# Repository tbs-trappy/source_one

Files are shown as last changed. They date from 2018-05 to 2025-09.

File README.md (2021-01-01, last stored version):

# source_one
Open Source FPV Drone Frame project initiated by Team BlackSheep
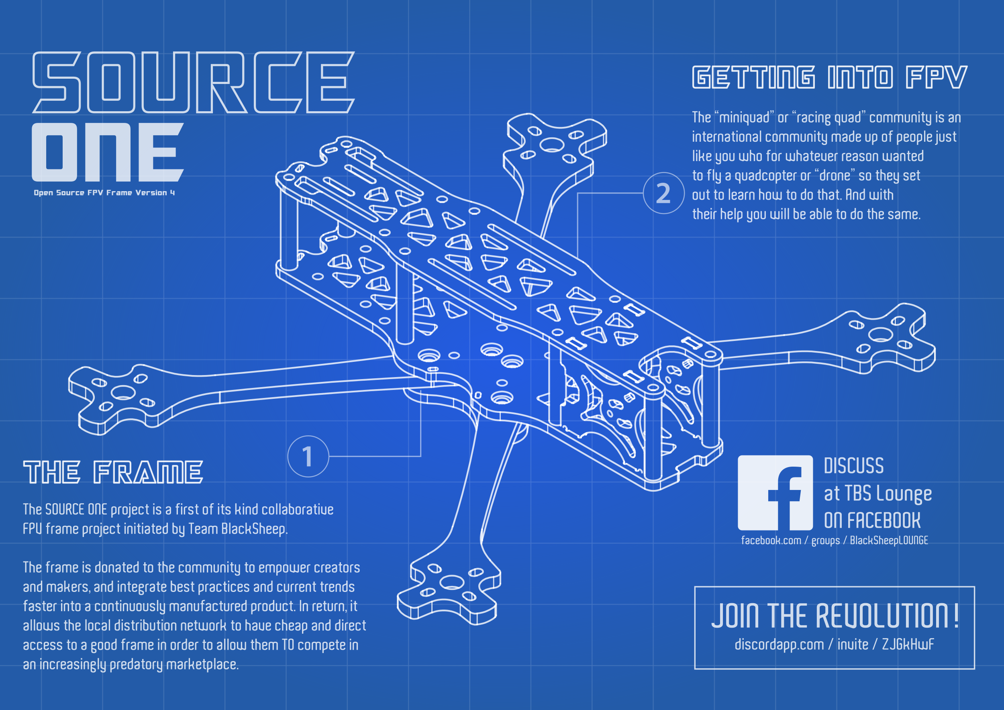
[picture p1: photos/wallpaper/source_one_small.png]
[](https://github.com/tbs-trappy/source_one/blob/master/photos/wallpaper/source_one.png)

# About SOURCE ONE
## The idea
The SOURCE ONE is the first of its kind, open source collaborative frame project. It empowers the community to integrate best practices and current trends into a continuously manufactured FPV frame. The price, documentation and compatibility puts it on track to be the most accessible frame for newcomers and professionals alike.

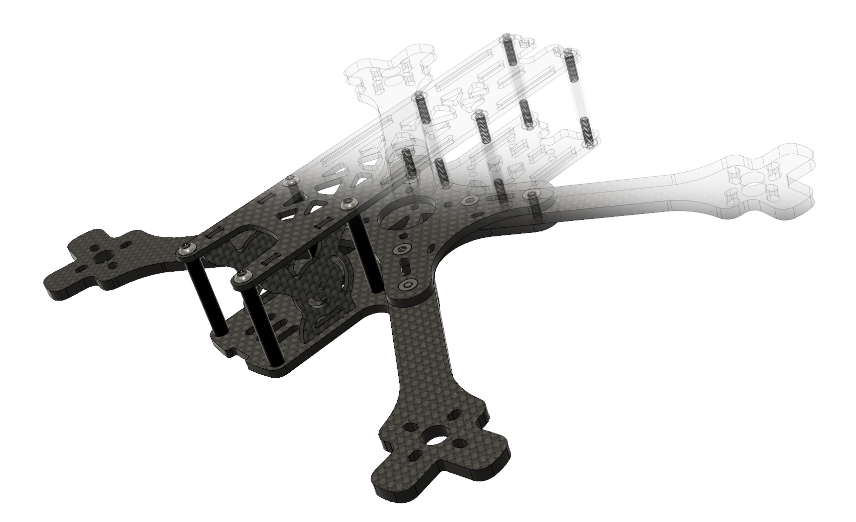
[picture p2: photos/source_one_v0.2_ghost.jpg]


## Frame specifications
* Wheelbase 5": 226mm
* Wheelbase 7": 318mm
* Top plate: 2mm
* Bottom plate 3mm
* Standoff height: 30mm
* Arm thickness 5": 4mm
* Arm thickness 7": 6mm
* Stack mounting: 30.5 × 30.5mm & 20 x 20
* Weight 5": 99.5g

## Hardware
* 24x M3x10 allen screw
* 4x M3x14 allen screw
* 8X OD 5mm M3 30mm standoff
* 6x M3 press insert nut

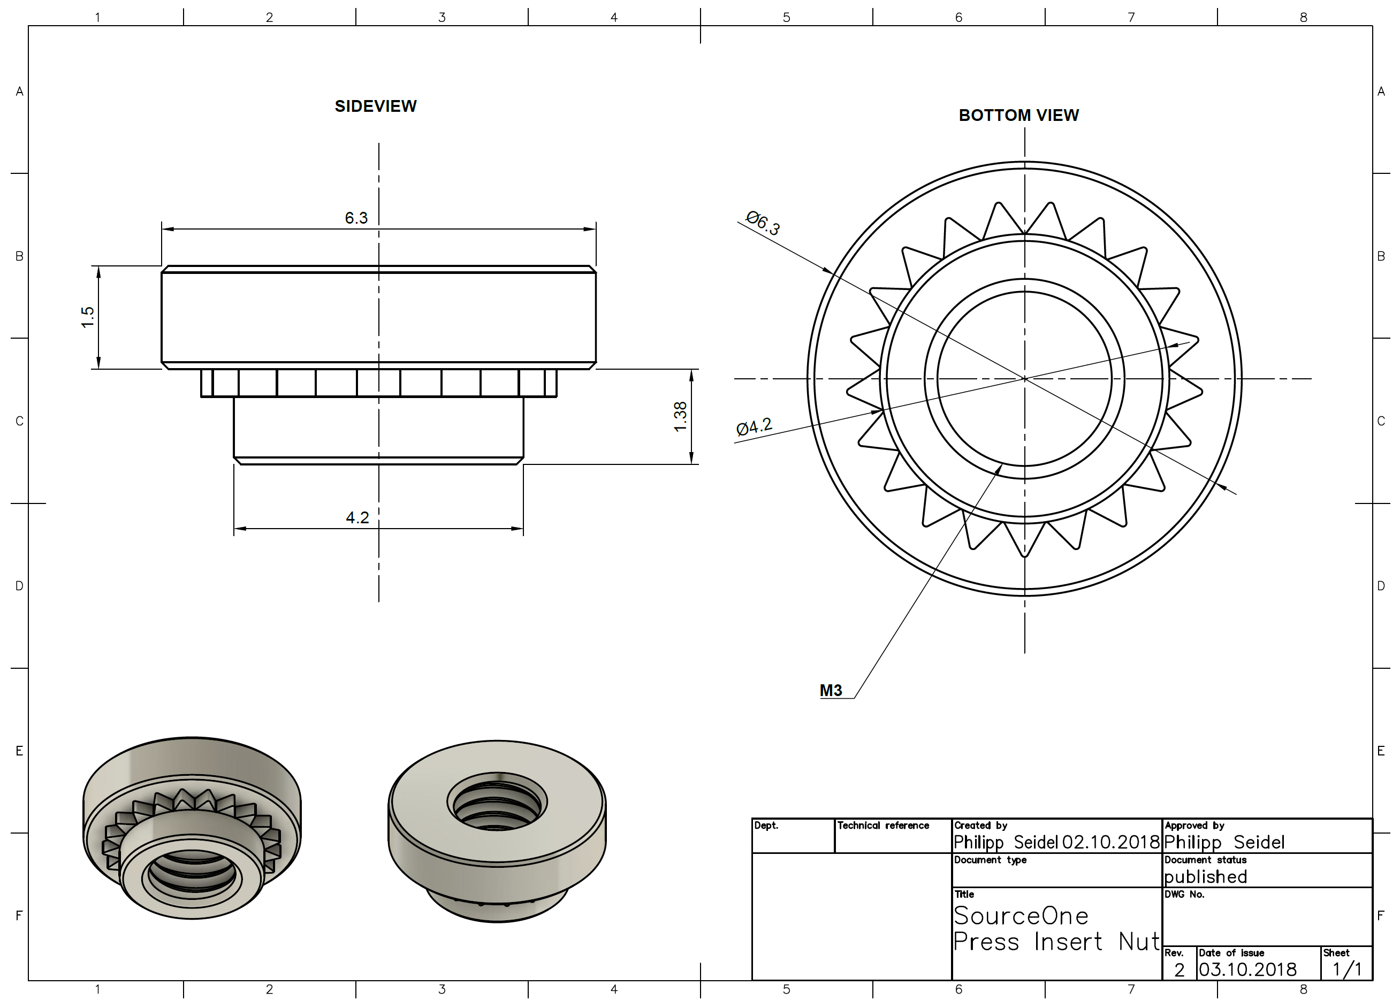
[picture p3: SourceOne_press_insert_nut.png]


## Project links
* Project discussion: https://discordapp.com/invite/ZJGkHwF 
* Project files: https://github.com/tbs-trappy/source_one 
* 3D-printed accessories: https://www.thingiverse.com/tag:sourceone

Please use the tag "sourceone" when uploading files to thingiverse.com

## Where to buy
* [www.team-blacksheep.com](https://team-blacksheep.com/products/prod:source_one_5in)
* [www.racequadgear.de](https://www.racequadgear.de/TBS-SOURCE-ONE-5)
* [www.n-factory.de](https://n-factory.de/TBS-SOURCE-ONE-5)
* [www.redbee.de](https://redbee.de/TBS-Source-ONE-5-VXXX)
* [www.defiancerc.com](https://www.defiancerc.com/products/tbs-source-one-5-v0-11)
* [www.ka-nickel.eu](https://ka-nickel.eu/produkt/tbs-source-one/)
* [www.phaserfpv.com.au](https://www.phaserfpv.com.au/products/tbssourceone5framekitv011)
* [www.multirotorshop.com](https://www.multirotorshop.com.au/product/tbs-source-one-v0-2-5inch/)
* [www.shop.brickracing.com](https://shop.brickracing.com/TBS-Source-One-V0.2-drone-frame)
* [www.skanehobby.se](https://www.skanehobby.se/shop/tbs-source-one-v0-2/)
* [www.juampifpv.com](https://www.juampifpv.com/index.php?pagina=detalle&idp=403)
* [www.killadrones.co.nz](https://www.killadrones.co.nz/store/TBS-Source-One-5-Inch-Frame-p137993332)
* [www.quadjunkie.co.nz](https://quadjunkie.co.nz/product-category/racing-freestyle-frames/tbs-source-one/)
* [www.drone-fpv-racer.com](https://www.drone-fpv-racer.com/en/dfr-source-one-5-frame-v3-3579.html)
* open [issue](https://github.com/tbs-trappy/source_one/issues/new) if you want your shop added

## Where to buy 3D printed parts
Here is a list of recommended 3D Printing services who are sharing their files under the GPL license (OpenSource). 
* [3dmatisse USA](http://bit.ly/3dmatisse_USA)
* [bmc3d.co](https://bmc3d.co/collections/all/source-one)

## Compatibility

| Part | v0.1| v0.11| v0.2| v3| v4|
| --- | --- | --- | --- | --- | --- |
| topplate |fits only v0.1 | | |fits all lower versions|fits only v4 | 
| bottompate |fits only v0.1 | |fits all lower versions|fits only v3 |fits only v4 | 
| arms | | | |fits all lower versions |fits only v4 | 
| centerplate |fits only v0.1 | |fits  v0.11 and v0.2 |fits only v3 |fits only v4 | 
| camplates |fits only v0.1 | | |fits all lower versions|fits only v4 | 
| battery pad |no pad available | |fits all lower versions|fits only v3 |fits only v4 | 

## Changelog
### SourceOne v4
* complete redesign
* DJI Airunits fits in the back

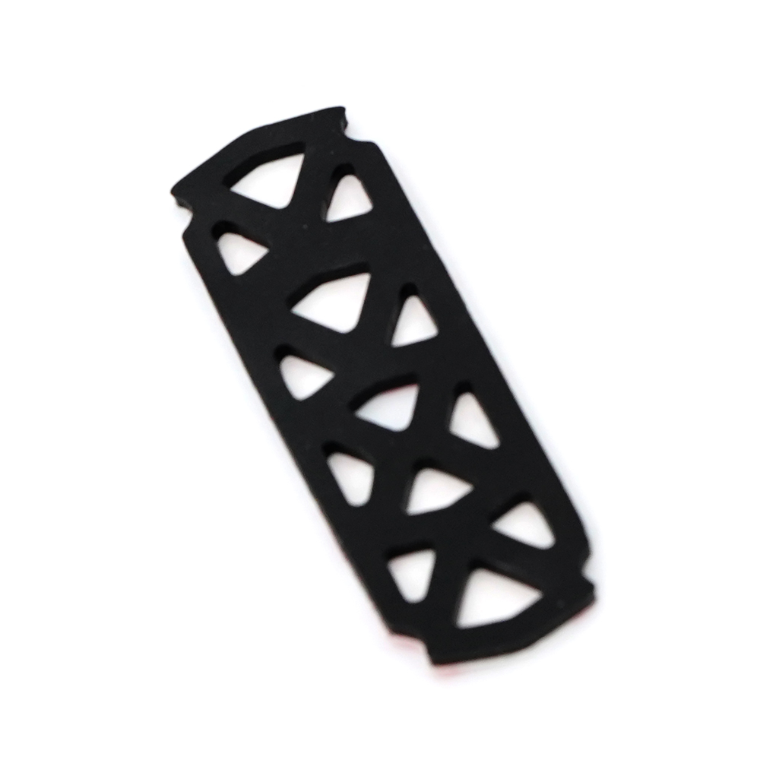
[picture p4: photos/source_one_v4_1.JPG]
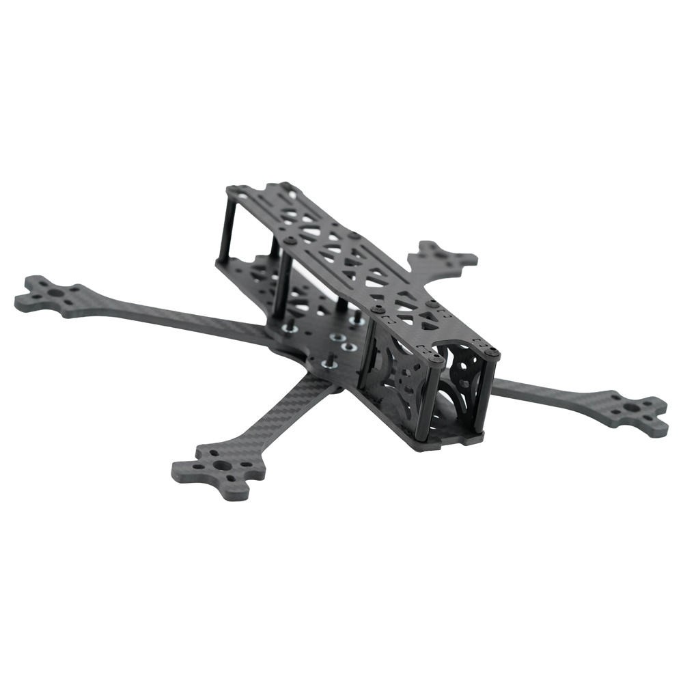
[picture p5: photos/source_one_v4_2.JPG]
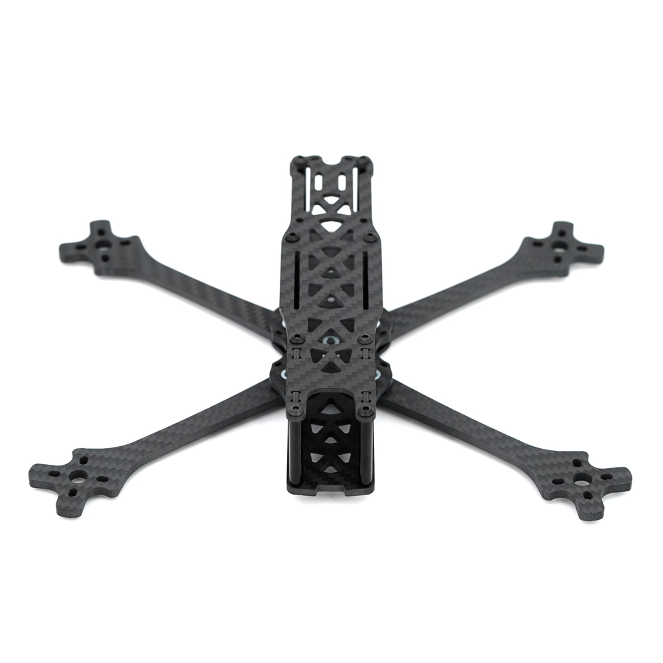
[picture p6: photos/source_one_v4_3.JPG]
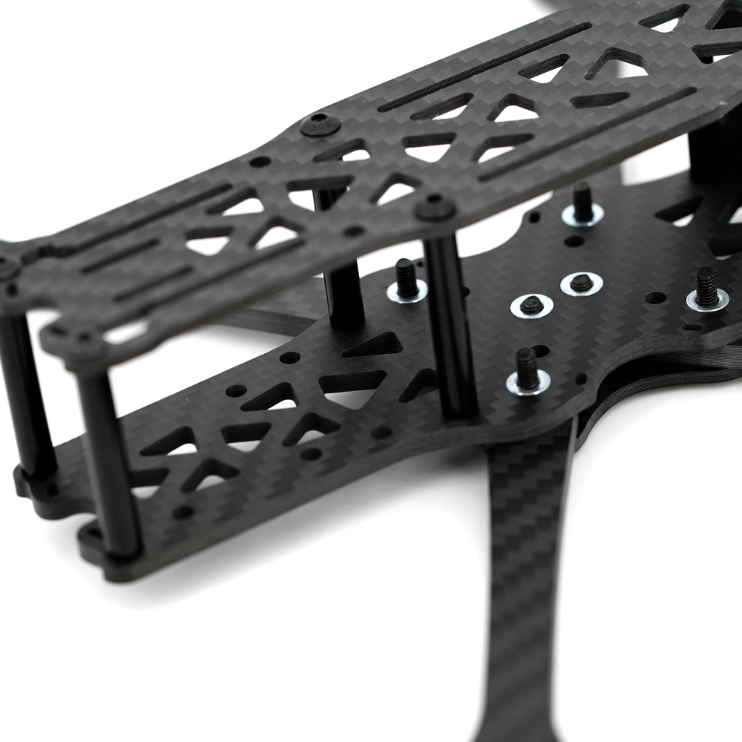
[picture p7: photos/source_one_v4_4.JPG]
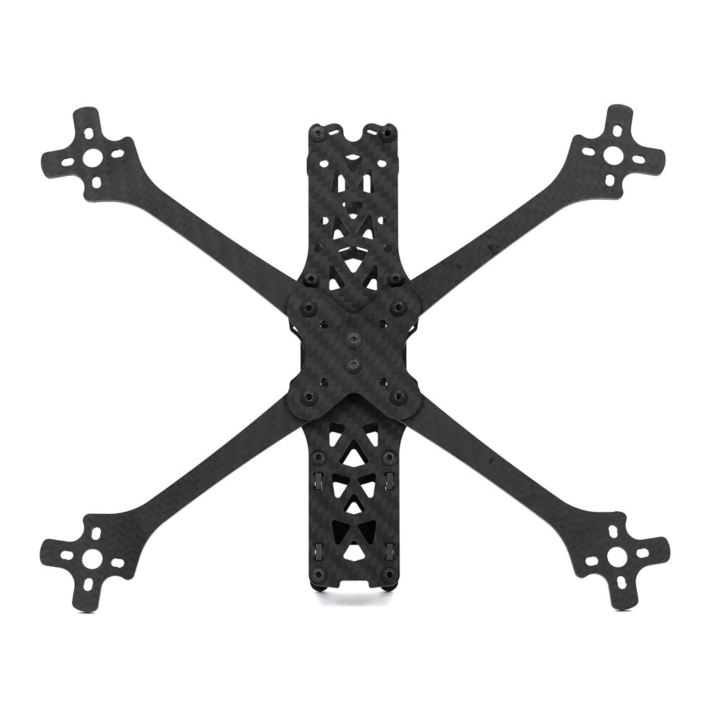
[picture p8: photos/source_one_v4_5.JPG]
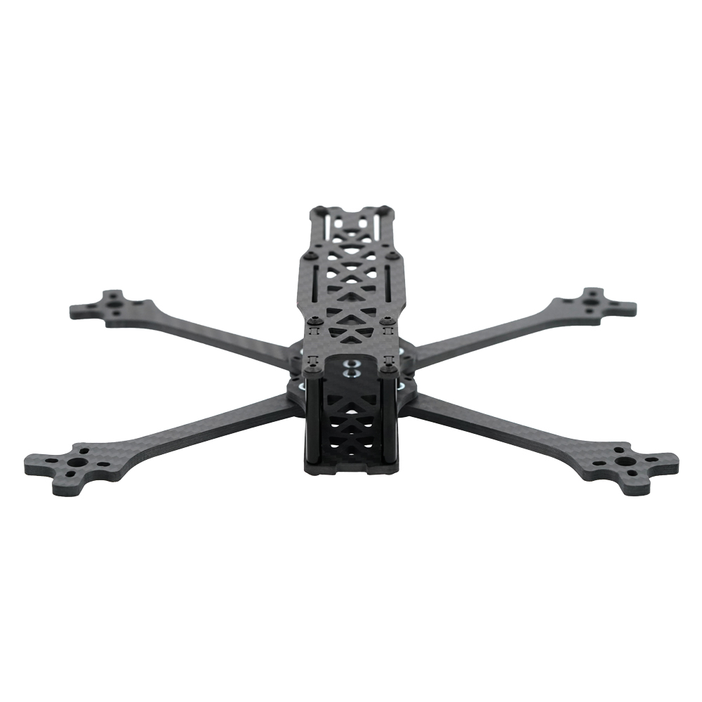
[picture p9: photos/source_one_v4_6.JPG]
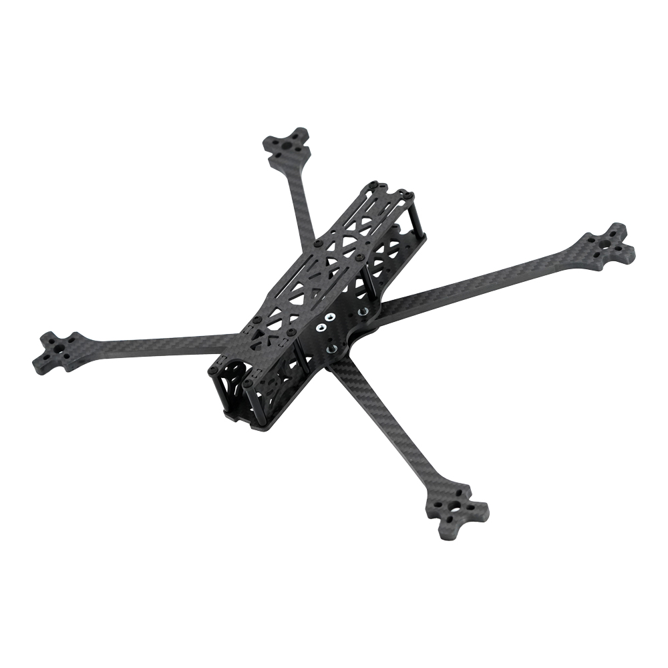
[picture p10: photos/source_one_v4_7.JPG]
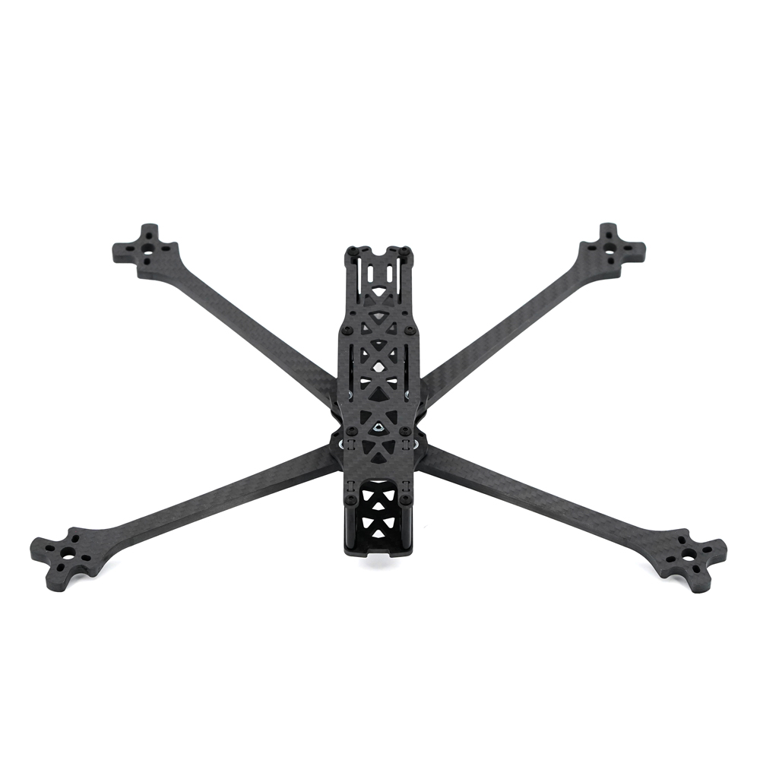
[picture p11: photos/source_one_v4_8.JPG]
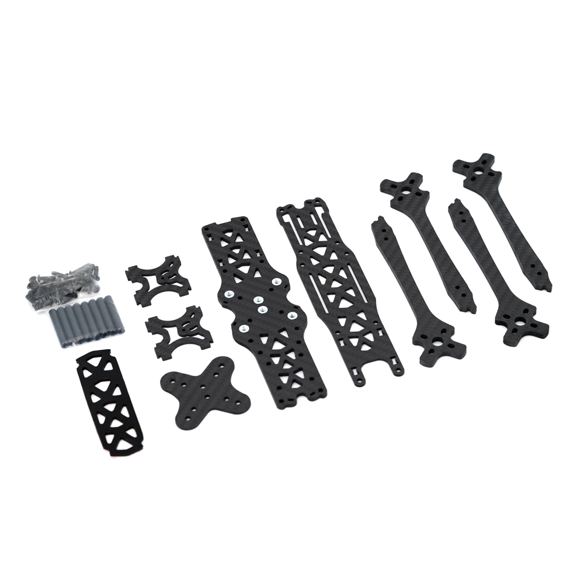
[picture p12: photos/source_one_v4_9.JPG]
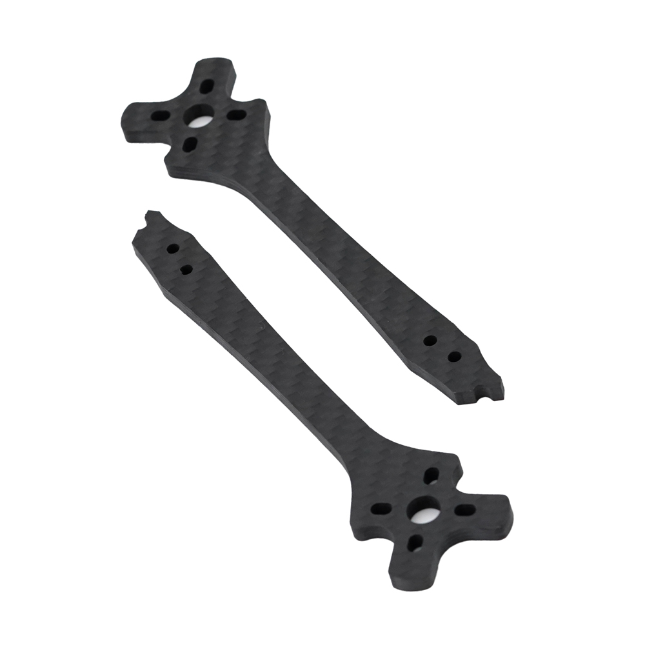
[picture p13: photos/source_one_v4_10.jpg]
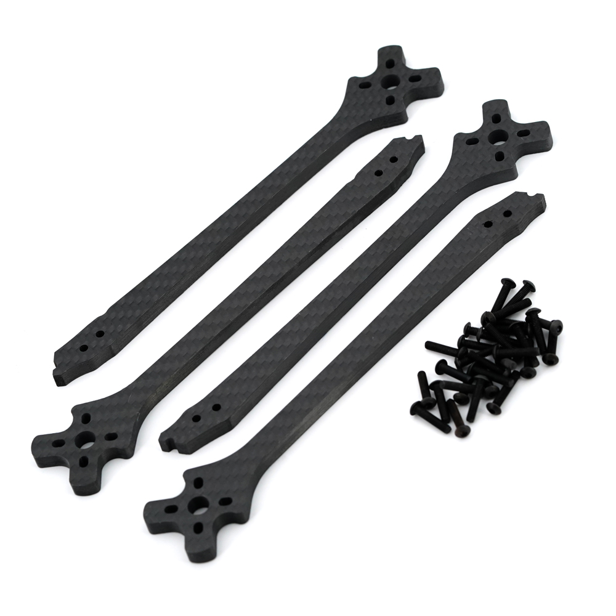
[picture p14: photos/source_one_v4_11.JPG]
          

### SourceOne v3
* new TopPlate, with longer Battery-strap slots - backwards compatible to V0.2
* new BatteryPad, cause of the repositioning and longer Battery-strap slots - NOT backwards compatible to V0.2
* new Cam-plate design, with Angel holes and a forward position, the Plate also contacts the 4 front Spacers for more rigidy in the front part - backwards compatible to V0.2
* Main-plate is now on top for more building room, a 20x20 (M2) mounting pattern added in the front, Antenna Zip-tie holes added - NOT backwards compatible to V0.2
* 5inch Arms got a reinforcement on the outer mounting hole (backwards compatible to V.01 and V0.2)
* new Bottom-plate - NOT backwards compatible to V0.2
* changed our versioning because its sounds better (we went from v0.2 straight to v3) 

that's all changes on the Carbon and the BatteryPad. For the guys that want to mount the Battery on the bottom, i made a small 3D-batterystrap mount, that also gives the battery a flat mounting option, cause of the swap of the Center and Bottom plate. All other 3D-Printed parts will fit the Version 0.3.

### SourceOne v0.2

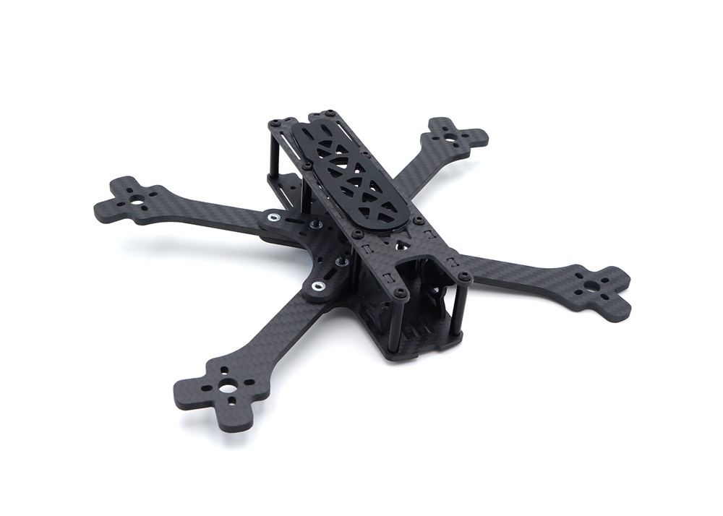
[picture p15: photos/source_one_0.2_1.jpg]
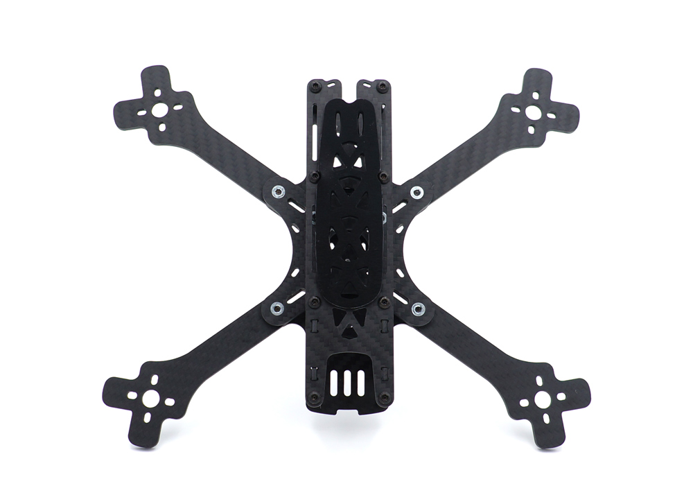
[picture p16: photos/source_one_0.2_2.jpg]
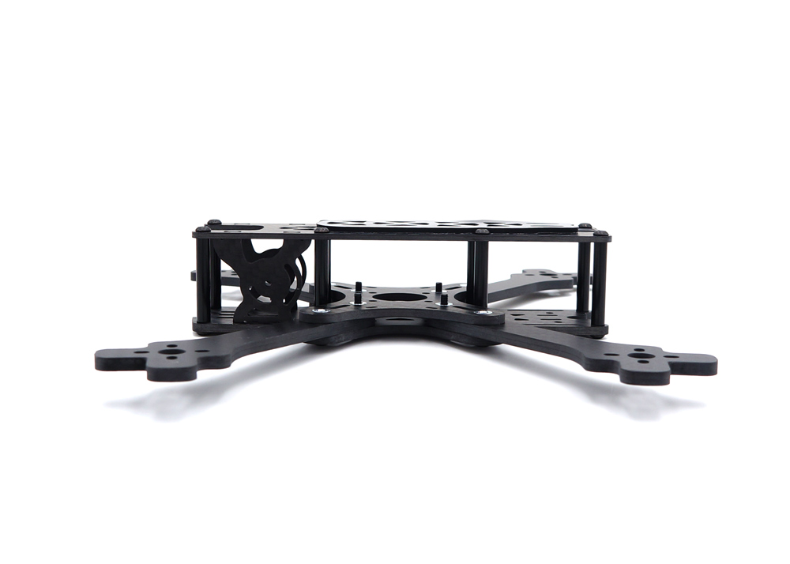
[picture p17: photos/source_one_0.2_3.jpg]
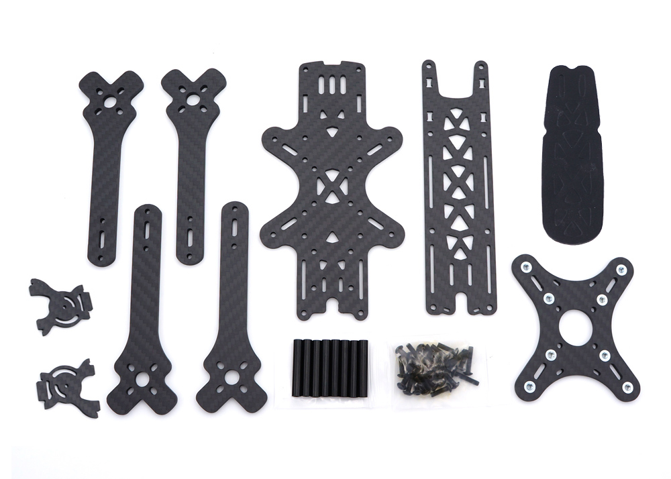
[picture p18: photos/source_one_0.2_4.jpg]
    

* top plate: new design pattern
* top plate: wider battery strap slots
* top plate: removed indentation near the second spacer row
* top plate: ziptie holes for RX Antennas
* center plate: ziptie holes for securing battery cable
* cam plate: new design
* added slots for MicroCam metal brackets
* bottom plate: micro cam bracket mounting slots
* bottom plate: 20x20 VTX stack holes
* 20x20 FC support
* arms: better motor protection
* arms: added 6 inch arms
* bottom battery mount slots for 20mm straps
* Impulse RC Wolf PDB support
* added silicone/foam battery pads (top & bottom)

#### compatibility
We changed the camera plate. Therefore topplate and bottomplate are not compatible with v0.11. Amrs and centerplate is compatible with v0.11

### SourceOne v0.11
* added press nuts
* define project leads and github commit rules
* define folder structure for acessories, variants, etc.
* define responsible people for maintaining manual, github website, graphics

### SourceOne v0.1

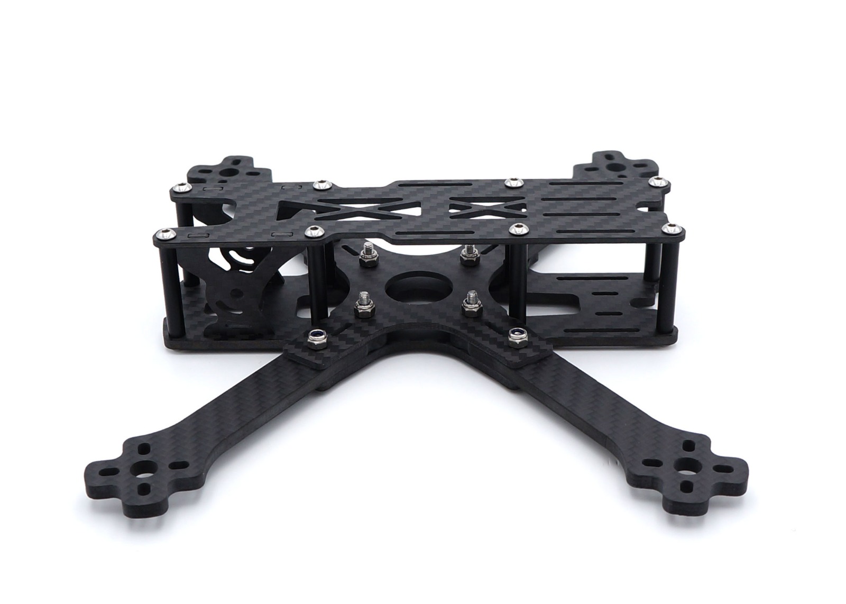
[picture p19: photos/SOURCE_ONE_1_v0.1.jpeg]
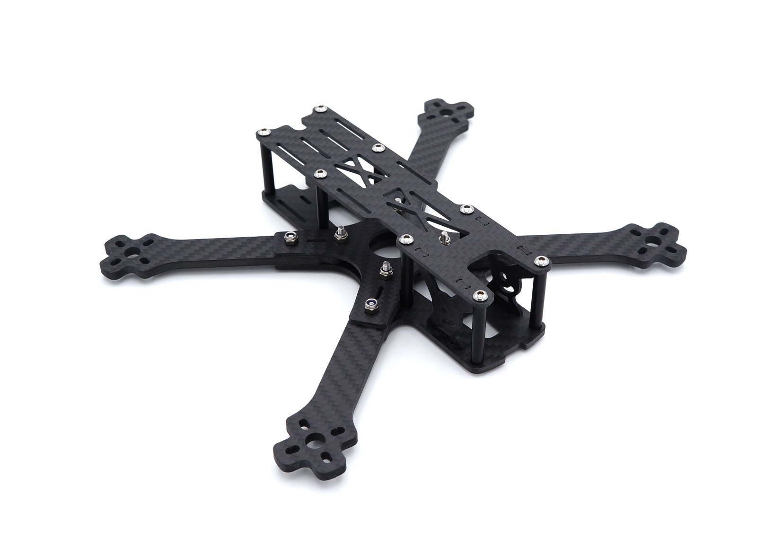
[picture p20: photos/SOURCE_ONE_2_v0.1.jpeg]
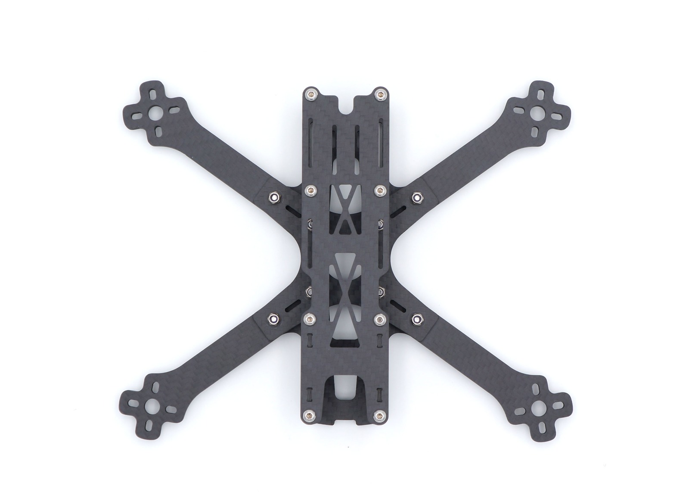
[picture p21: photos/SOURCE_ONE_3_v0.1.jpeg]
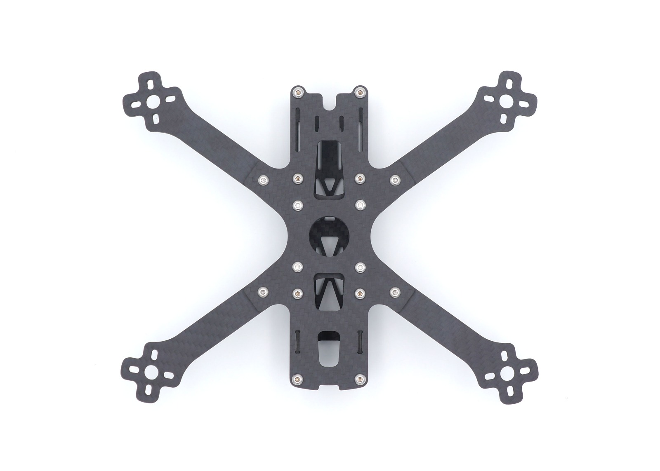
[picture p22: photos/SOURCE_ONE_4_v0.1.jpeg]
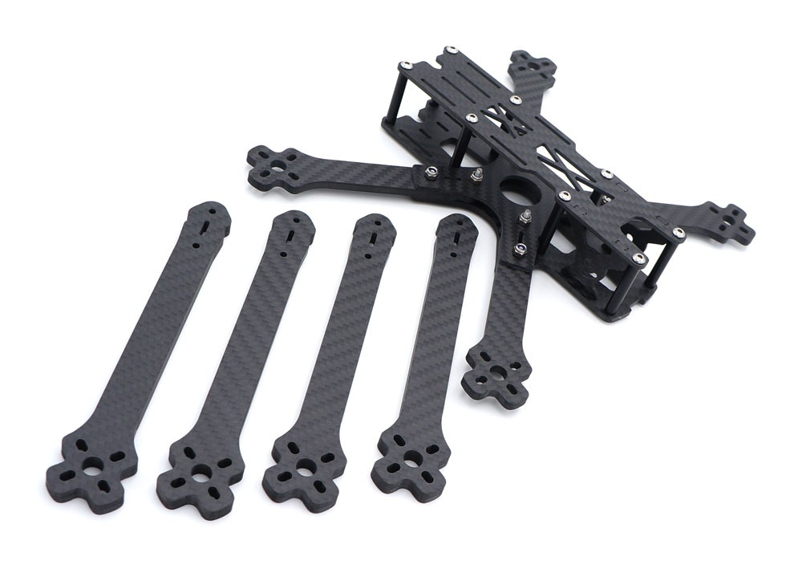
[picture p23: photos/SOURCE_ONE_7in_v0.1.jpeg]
    

* initial release from TBS

## Project license
The frame files are released under GNU Public License (GPL) V3. More information here: https://www.gnu.org/licenses/gpl-3.0.en.html 

## Project naming requirements
SOURCE ONE is the name of the frame. If you are thinking about manufacturing it, you are expected to prefix the name with a brand name in order to allow customers to distinguish the different manufacturers, e.g. “TBS SOURCE ONE”. As a manufacturer you are also expected to denote the version number of the frame files that you have placed as basis of the project, e.g. “TBS SOURCE ONE V0.1”. 
If you have forked the project, you need to give it another name in order to avoid confusion between SOURCE ONE and your project.
Accessories from the SOURCE ONE project also need to be named with the entire prefix, e.g. “TBS SOURCE ONE FPV Camera Adapter”. Unless the file is not compatible with certain versions of the frame, the compatible version number or version range also needs to be included in the name, e.g. “TBS SOURCE ONE FPV Camera Adapter V0.1 - V2”

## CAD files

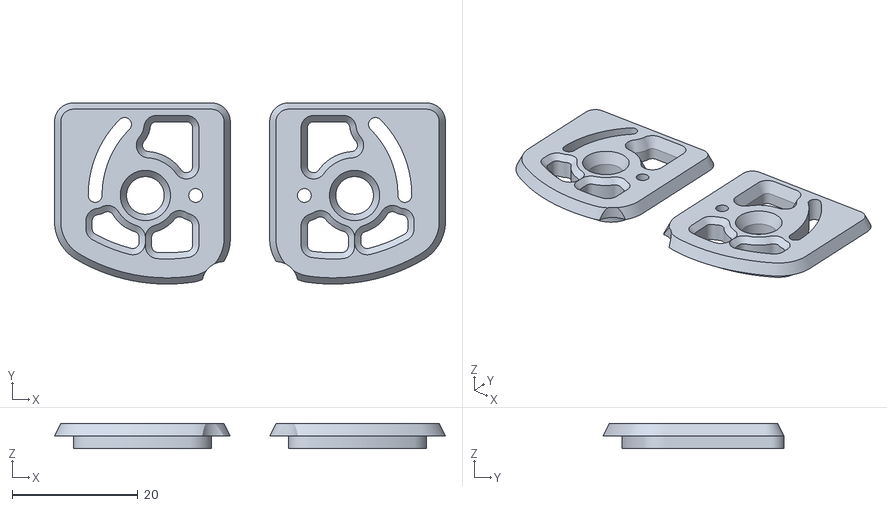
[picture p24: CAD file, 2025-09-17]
SO1-V6-O4-Cam-Mount.stl
62.3 x 28.8 x 4.00

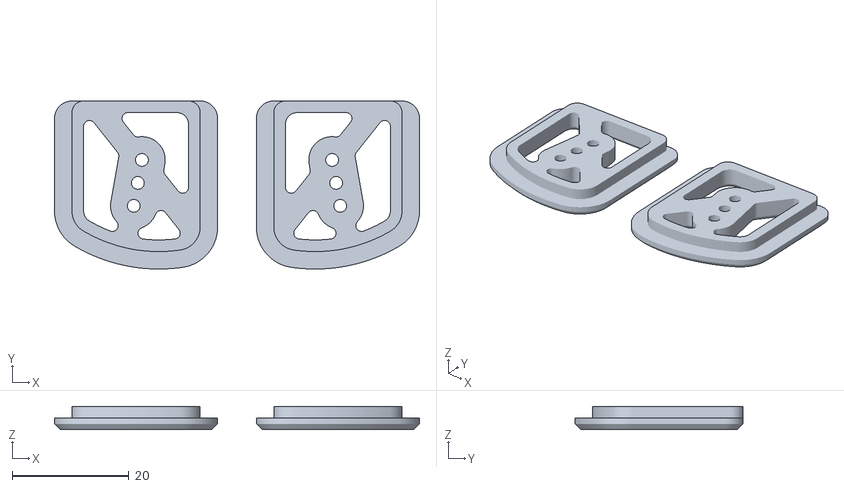
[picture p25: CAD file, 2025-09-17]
SO1-V6-AN-Cam-Mount.stl
62.6 x 28.8 x 4.00

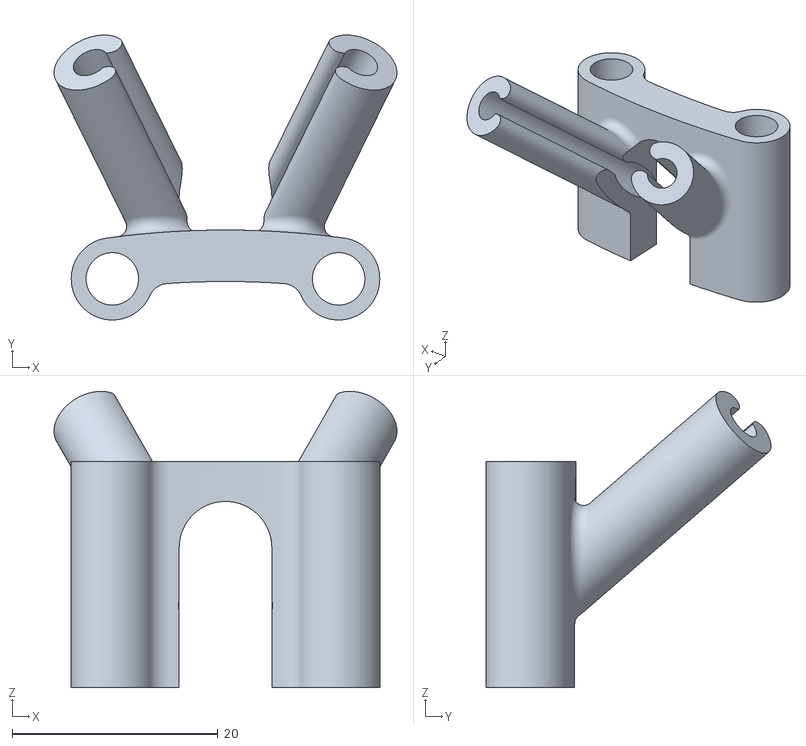
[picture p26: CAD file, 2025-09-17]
SO1-V6-O4-Antenna-Mount.stl
33.3 x 27.7 x 28.8

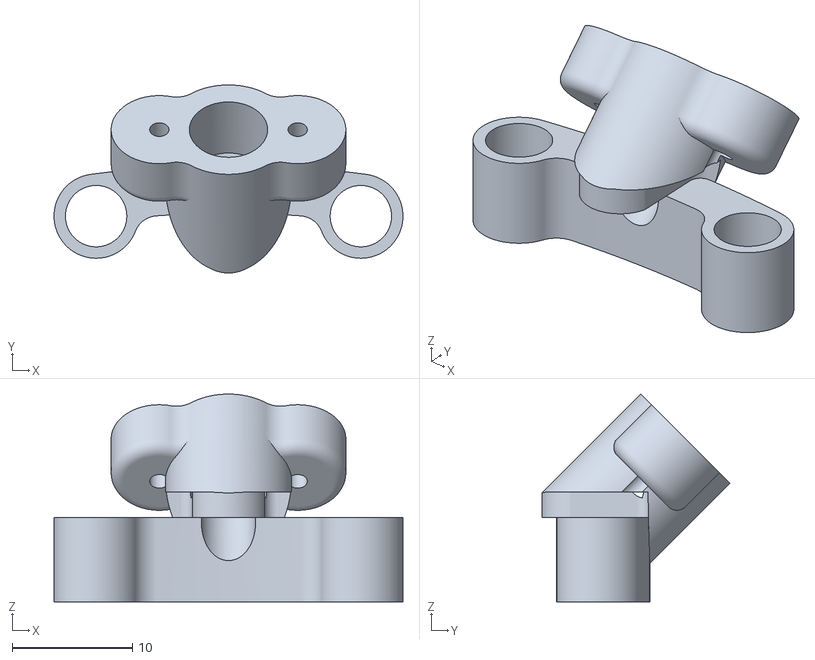
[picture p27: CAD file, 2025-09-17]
So1-V6-2025-SMA-mount.stl
29.0 x 15.6 x 17.3

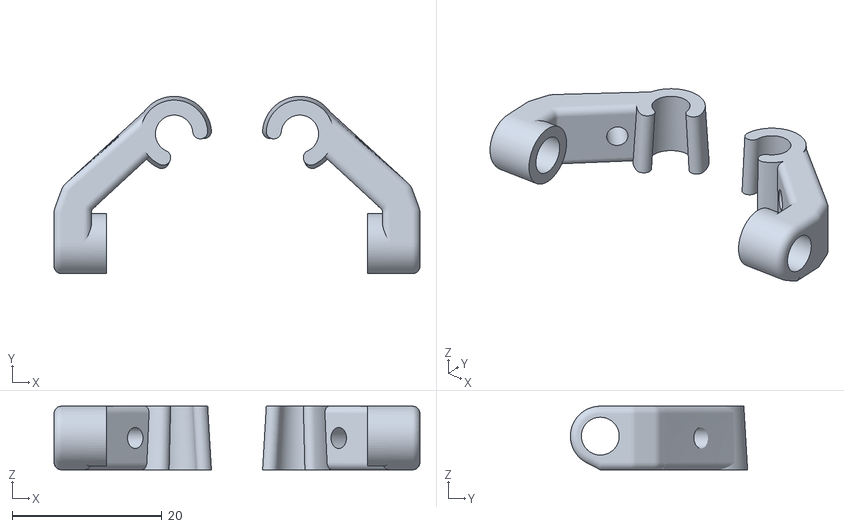
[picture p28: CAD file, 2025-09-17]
SO1-V6-ImT-Mount.stl
48.9 x 23.7 x 8.50

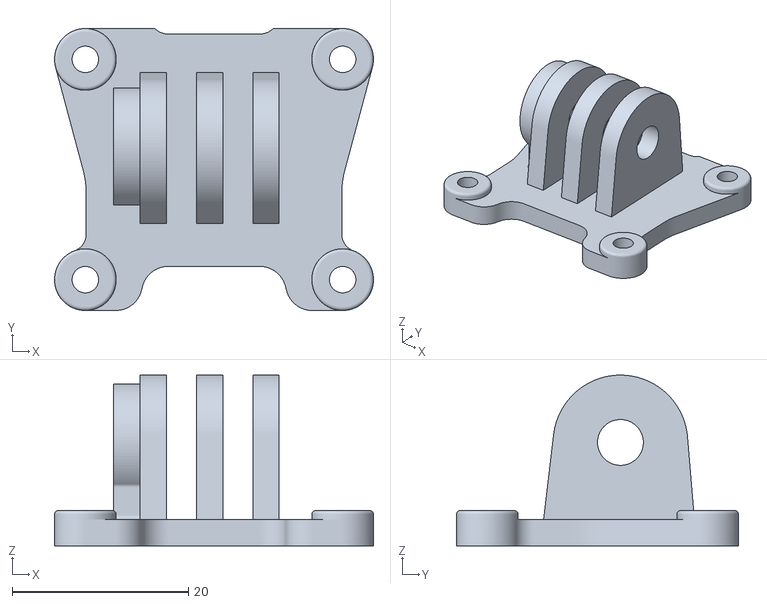
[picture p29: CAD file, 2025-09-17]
SO1-V6-GoPro-Mount.stl
36.2 x 32.0 x 19.4

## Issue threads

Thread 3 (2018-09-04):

Camera screw hole too large

drdrenz, 2018-09-04:
Camera hole is 3.8mm in diameter, would be better is it was 2mm.  updated design attached to rectify.
[SOURCE ONE camera hole 2mm.zip](https://github.com/tbs-trappy/source_one/files/2350220/SOURCE.ONE.camera.hole.2mm.zip)

ps915, 2018-09-04:
thanks for your submission. We already changef this in the next version (0.2) which will be released in a few days.

I will close the issue, but keep your file online if anyone wants to download it.

Closed 2018-09-04.

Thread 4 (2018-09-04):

Source One Killa Drone Arms

drdrenz, 2018-09-04:
Modified Arms to allow for better motor protection for larger motors
[SOURCE ONE Killa Drones 5.5 inch arms.zip](https://github.com/tbs-trappy/source_one/files/2350236/SOURCE.ONE.Killa.Drones.5.5.inch.arms.zip)
 and to allow for my favorite props size 5.5 inch...

ps915, 2018-09-04:
thanks for your submission. We already changef this in the next version (0.2) which will be released in a few days.

I will close the issue, but keep your file online if anyone wants to download it.

Closed 2018-09-04.

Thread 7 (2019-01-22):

Possibility or problems with making a "slammed" ?

sense-amr, 2019-01-22:
Since these really low CG rigs are all the go these days .. and i have to admit i really enjoy my alien 5" "slammed" .. i was wondering if there is any structural issues regarding the frame .. to using shorter standoffs to make a slammed Source?

ps915, 2019-01-23:
You will loose the ability to use the camera plates which are also a stuctural part. I dont think there are structural issues when you use smaller standoffs and use long screws for the first 4 standoffs!

Feel free to report back your findings, if you use the frame "slammed"

sense-amr, 2019-01-23:
Ahh .. will that camera mount support an HS1177?

ps915, 2019-01-23:
Yes, but not when you have smaller standoffs

sense-amr, 2019-01-23:
i might have to make an issue to have the frame support .. Slammed Standoffs.. and have an alternative camera mount made for it :)

sense-amr, 2019-01-23:
are you flying a source one? ..

Closed 2019-01-23.

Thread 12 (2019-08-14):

Why is this frame so heavy?

daimondgeezer, 2019-08-14:
Is there any way to get this frame lighter? I like everything about it except the weight.

ps915, 2019-08-15:
Our goal was to build a strong frame, so we didn't really care so much about the weight. Of course there are plenty of things we could do, to save some weight, but we may have to remove some features and thinner some plates.

If you have any idea on saving weight, tell us and we can talke about it.

daimondgeezer, 2019-08-15:
Thanks for your reply. I plan to use this frame as my next build. Will probably get rid of the camera mounting plate and slam it with some lower standoffs.

tobiasbischoff, 2019-08-15:
I recently build one and was thinking the same. There is a ton of Carbon in it. The Bottom Plate and the lower Sandwich plate are probably too thick. You could probably get away with much thinner plates out of high quality carbon here. I would not recommend getting rid of the camera plates, the add a lot of structural integrety in the front. I would rather switch to aluminium hardware in the non structural areas.

daimondgeezer, 2019-08-15:
Thanks a lot for your input. Will give this frame a go after I break the next boomerang arm on my Flosstyle. It looks like a tank 🙂

fpvg, 2019-09-08:
well i can attest. I bought this frame thinking it was going to be better. And it hasn"t broke yet, some scuffs on the arms from concrete i see a arm delaming on the edge but hell, this thing has been to hell and back far more than my old lighter clone frame, and still going strong tell this day. in the begining , everything breaks but this frame, lol. not that it cant be broken , but man id pay to see that. maybe ill make a video challenge

fpvg, 2019-09-08:
leave it alone for us, bashers, make a lighter race version for the speed junkies,lol

Closed 2019-09-18.

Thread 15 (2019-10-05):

Toilet tank slot

Ryano12, 2019-10-05:
It would be nice to see the top plate designed to allow for a single toilet tank strap.. Centre line of battery aligning with the centre line of the props.

Closed 2021-01-24.

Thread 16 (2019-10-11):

Bad Positioning Of The Press Nuts

drlocke, 2019-10-11:
I like the idea of having more space for higher stack towers or whatever, but WHY were the press nuts placed on the bottom plate instead of the sandwich plate as in the previous version?
The point here is that you want the screws to stick out at the top to screw the stack on it. If you don't need the extra space from the v3 version and want to build the frame with a lower center of gravity like you was able in v2, you can't do this without a set of extra M3 nuts.
That's a shame, because this problem would have been very easy to avoid by placing the press nuts on the sandwich plate. This can be placed either above the base plate or below the base plate and in both cases would allow the screws to protrude upwards and the stack to be fastened without additional tools.

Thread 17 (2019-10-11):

Sticky Pad Doesn't Fit Correctly

drlocke, 2019-10-11:
The sticky pad has two cavities for the two screws on the top plate. These cavities no longer correspond to the position of the screws in v3. At least not if one assumes that the cut-out pattern of the sticky pad should correspond to that of the top plate.

ps915, 2019-10-15:
When we released V3, TBS did not grabbed the new file for our new battery pad. So they produced the wrong one.

But: you can use those battery pads, anyway. Just make new cutouts for screws (red circles)
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

Closed 2019-10-15.

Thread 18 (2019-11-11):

Cutting

mpbgodinho, 2019-11-11:
I have a CNC machine, wich is the best milling cutter to DIY the frame?

Many thanks

ps915, 2019-11-29:
I don't have any CNC cutter at home but had the chance to lean CNC cutting a bit during my job.
Diameter of the milling tool: check the files and search for the smallest inner radius. Thats your diameter for the milling tool. Outer radius can of yours be milled with lager tools, but then you have to change tools of course.

i used these tools for carbon fibre: http://www.brokking.net/images/carbon_fiber/carbon_fiber_04.jpg

Closed 2021-01-24.

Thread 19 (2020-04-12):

Dji Air Unit compatibility

marcelinojorgeromero, 2020-04-12:
Is there any plan to make the frame compatible with the dji air unit? From what i saw it needs around 4 to 5 millimeters between the stand offs in the back.
thanks

ps915, 2021-01-24:
V4 is now compatible with AirUnit!

Closed 2021-01-24.

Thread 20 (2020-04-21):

Name of Frame

ObstacleTAKUYA, 2020-04-21:
Hello,
im currently working on a complete Rework of the Frame. Less High, built in gopro mount and so on.
When its done, id like to sell it on armattan Productions or even manufacture it myself. Am I allowed to do that and name the Frame something like  "Takuya´s NAME " or does it have to be Takuya´s Source One Version X.X
Cheers

tbs-trappy, 2020-04-21:
if there is no resemblance you can call it whatever, as long as attribution is given. if it's exactly the same thing, then the SOURCE ONE name should prevail.

ObstacleTAKUYA, 2020-04-21:
okey great! one thing i need to ask though. Where can i get these pressnuts from?
Do you know if armattan productions has these?

Closed 2021-01-24.

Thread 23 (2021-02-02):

No documentation for V4 assembly

Matthew-Beckett, 2021-02-02:
There is no documentation for assembly of the V4 frame.

ps915, 2021-02-02:
What is your question regarding the assembly?

Matthew-Beckett, 2021-02-02:
Hi Phillipp,

I am experiencing not necessarily an issue but a concern with how the V4 sandwich plate mounts to the bottom plate. The shorter M3 screws supplied with the retail variant only expose a minimal amount of thread for my flight controller standoffs to mount to, I am concerned this will break free in flight or in a crash.

Furthermore, switching to using the larger screw results in too much thread being exposed above the bottom plate and the anti-vibration standoffs not sitting flush with the frame.

Also, since the redesign of the sandwich plate, I am confused about the use of the two most central threaded posts. Do I use these to secure the plate further to the bottom? My stack is 30.5mm and at the moment my arms are only secured with the outermost screws into the threaded inserts as the inner ones are not threaded and I can only assume is used by the long M3 screws to mount a smaller flight stack.

However, all of this speculation as to how it goes together, what each mounting hole is for, and which screws to use during my first build has led to quite a lot of frustration and considering the assembly of the V3 variant was quite well documented I am disappointed the same love has not been given to the redesigned variant.

Especially when it's so different to a noob like me from previous iterations. If I was to follow the V3 instructions for mounting the sandwich plate and arms I would have one screw per arm secured in the threaded insert and the second screw would just be push fit into the bottom plate's hole and held in by nothing more than friction.

krunked-fpv, 2021-02-02:
long screws on outside, shorer on inside, use nylon standoff. done.

On Tue, Feb 2, 2021 at 1:38 PM Matthew Beckett <notifications@github.com>
wrote:

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

Matthew-Beckett, 2021-02-02:
Do I still need the shorter on the inside with a 30.5mm stack? There's nothing for the inner ones to thread into, and the longer ones push the standoffs too high which came with my F405-STD

krunked-fpv, 2021-02-02:
nope just use long ones on the outside and screw in nylong standoffs. use
short ones on center.
my s1 v4 is slammed to 20mm and i have plenty of room.

On Tue, Feb 2, 2021 at 1:55 PM Matthew Beckett <notifications@github.com>
wrote:

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

Matthew-Beckett, 2021-02-02:
@ps915 would you accept a PR with V4 instructions? @krunked-fpv thank you so much!

Closed 2021-05-10.

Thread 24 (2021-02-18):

Arms of V4 delaminate

cwei, 2021-02-18:
After a baby crash into a field (mud) the front arm is delaminated like puff pastry.
Nearly every layer of carbon came off.

Is it a quality problem of the carbon or are the 4mm too weak?
Or both?

I had no issues with the V3.

cwei, 2021-02-18:
Here is another example https://www.youtube.com/watch?v=Xlhkx9ak-zo

cwei, 2021-03-12:
Replaced the original 4 mm arms with 5 mm arms. (thanks Kai for cutting)
Now the quad flies like a charm.
No torsion and bending of the arms any more.
The vibrations and oscillations are gone.

krunked-fpv, 2021-03-12:
yeah i have a 5mm version and 6mm version -- 6mm version flies best imo :)

On Fri, Mar 12, 2021 at 4:53 PM Carsten Weiße ***@***.***>
wrote:

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

cwei, 2021-03-19:
This cool [frame resonance analysis](https://www.youtube.com/watch?v=-W7RzZ66eRo) of the S1 V4 shows why it flies better with thicker/stiffer arms.

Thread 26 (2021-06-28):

Brimg back the v4 features, drop the flawed HD arms

noahwaldner, 2021-06-28:
The V4 is a stellar fram, great flight performance, very rigid, good compatibility

With the transition to the HD the improvements from v3 to v4 were lost again.

- Arms are wider again and have resonance
- The spacing from the front to the rear motors have a shorter spacing again -> More propwash

Can we please fix this and make a arm set wich is thinner (like the v4) (maybe thicker carbon for the crash-a-lot pilots)
This would improve the flight performance drasticly. If we make the arms slightly longer, so that a 5.55" prop radius would fit, we can get rid of most of the propwash.

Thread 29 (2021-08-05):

V4 DJIA Air Unit options

petertorelli, 2021-08-05:
Can you post some images of methods for mounting the DJIA Air Unit in the v4 frame? The space in the rear bottom is kinda crammed with the cap / power lines and RX. Looking for some tips that don't involve 3D printing. Maybe strapping it to the top rear plate and feeding the antennae through the long cuts? What do the pros recommend?

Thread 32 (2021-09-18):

Battery Pad Issues

Ryano12, 2021-09-18:
Hi There,

The current battery pad clashes with gopro mounts that utilise the front 4 standoff screws.
It also doesn't extend far enough back for the majority of battery packs.

I have attached a design that fixes both issues. However, I am not sure if the current design is constrained by silicone pad sheet sizes or something else along those lines.

Feel free to add the design/modify to suit if you deem acceptable
[SO1_V4_BatteryPad.zip](https://github.com/tbs-trappy/source_one/files/7190789/SO1_V4_BatteryPad.zip)
.

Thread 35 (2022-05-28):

Arm side plate for 7 inch

tinexd, 2022-05-28:
hi, do anyone have constructed source one HD 7 inch arm side plates like the flywoo explorer?

sicboy-fpv, 2023-10-03:
i made some. work very fine, frame is stiffer, less resonances, better tuneable.
@tinexd

sicboy-fpv, 2023-10-13:
download in my github

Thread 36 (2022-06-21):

Version 5

kingfisher09, 2022-06-21:
I'm very confused. A version 5 is talked about on a few sites but not mentioned anywhere on here. Does anyone know where I can find CAD of the version 5?

Livewire85, 2022-07-14:
Any updates? Ive got one of these on my bench desperately waiting for 3d printed parts...

folgoris, 2022-07-16:
It is a common practice now, for early versions they release the source code or CAD files to show more transparency and approval from the community, once it has entered the market they do not release any source code.
I hope that I'm wrong and they keep releasing the CAD files for newer versions.

Bananenbrot83, 2022-08-19:
Hi guys i just published my reverse engineered CAD files of the sourceone V5. Feel free to use it:
https://www.thingiverse.com/thing:5469653

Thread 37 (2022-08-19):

SourceOne V5 CAD Files

Bananenbrot83, 2022-08-19:
Hi I just made a SourceOne V5 in my CAD.

Feel free to use it : https://www.thingiverse.com/thing:5469653.

If you need another file besides step/stl and dxf feel free to contact me.

hprobst, 2022-12-21:
Thanks a lot for the model!

I could not find the 2 camera mounting plates. Is it possible that you add this parts to your model?

@all:
why is the SourceOne V5 model not here in this repository on github?

Bananenbrot83, 2022-12-21:
Hi,
thank you for your appreciation!
i am sorry that i forgot them. I will of course add them within the next days (it will happen this year !)
To download every file individual the printables link is better.

I will add the camera mounting to both links (printables & thingiverse)

UltiFix, 2022-12-28:
@hprobst For vis TBS v5 dxf files here, sent to me by TBS
https://github.com/UltiFix/source_one_V5

@Bananenbrot83 Thank you for modeling this, your model is actually nicer for me BECAUSE its in solidworks assembly, but I posted incase its useful for anyone.

Best,
Ulti

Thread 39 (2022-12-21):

V5: DJI O3 Air Unit compatibility

hprobst, 2022-12-21:
The camera mount and the front spacers are not wide enough for the new DJI O3 Air Unit.

I remixed the V5 model on thingiverse to fit the DJI O3 Air Unit camera:
https://www.thingiverse.com/thing:5730548

Would be great if you add DJI O3 Air Unit compatibility in SOURCE ONE V6.

UltiFix, 2022-12-26:
For a design thats supposed to be "open source collaborative frame project" its sad we have to resort to reverse engineered models on thingiverse (not a dis to the reverese engineer, thank you). But, keeping track of all the modifications to it are going to frankly be a nightmare.

Wonder if the guy who reverse-engineered it would be OK/allow/do a GitHub repo for it so changes such as yours can be tracked for others.

FlyHighFPV, 2025-09-16:
3 years later... we have v6! ;)

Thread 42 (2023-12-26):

Feature request/feedback - PDF drawings of mounting holes + please avoid odd off center/non-rounded dimensions in future designs

mbainrot, 2023-12-26:
Was working on designing a mount for my TBS Source One V4 and discovered a rather annoying thing whereby the inner main frame standoffs have two different offsets from center (center being the center of the 30.5x30.5 stack mounts), that being 32.25mm and 37.05mm front/back respectively.

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

I have not checked the V5 yet (I don't own one yet :) ) so apologies if this particular gremlin is already fixed in V5.

Please also provide PDF drawings showing the locations, sizes and offsets for your mounting holes too as it would make designing accessories a lot easier.

Whilst the DXFs do work, if you don't have high end CAD tools (or know how to use the open source ones in my case) deriving the measurements from DXF is a very fiddly and time consuming endeavor.

Cheers!

Ryano12, 2024-02-10:
They're still very random values.
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

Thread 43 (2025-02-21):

New version to accept 04

notice-fpv, 2025-02-21:
Existing TPU camera mount options are unacceptable.  Could a V6 be made to fit the 04 Pro?

Pyrolassist, 2025-03-07:
I was hoping for the same.  Is the Source One project no longer alive? There doesn’t seem to be much activity in the last year. O4 Pro Anyone?

notice-fpv, 2025-03-07:
Since this post hasn't gotten a lot of traction, I've actually been looking at version 3 which appears to be significantly wider

luci3D, 2025-04-04:
I just sent @tbs-trappy an email with my first model proposal, i dont own a source one or an o4 so Ill need people to try it out

ryantrax, 2025-04-14:
You can purchase an O4 conversion kit TPU set here:
https://www.aerial-pixel.com/dronepilots/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

luci3D, 2025-04-14:
I think buying this is not an acceptable solution buddy, people need a 3D file unfortunately

luci3D, 2025-04-14:
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

Last week I got a source one frame and one of my friends let me borrow an o4 cam, looks like the fit works, just gotta beef up more the bumper and change a couple things

ryantrax, 2025-04-14:
> 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
>
> Last week I got a source one frame and one of my friends let me borrow an o4 cam, looks like the fit works, just gotta beef up more the bumper and change a couple things

I was just offering a source. Not everyone 3D prints or can design a mount for the O4 camera, Air unit and new antennas.

Strykar, 2025-04-16:
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
https://www.printables.com/model/1244631-sourceone-v5-dji-o4-air-unit-pro-camera-mount

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
https://www.printables.com/model/1242871-sourceone-v5-dji-o4-air-unit-pro-antenna-mount

v3 - https://www.printables.com/model/1180917-dji-04-air-unit-pro-source-one-camera-mount

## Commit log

2018-05-21 PDF Overview (plate thickness)
2018-06-02 Add files via upload
    v0.1.1 release
    [SOURCE ONE v0.1.1.dwg, SOURCE ONE v0.1.1.dxf]
2018-09-27 v0.2 release
    [SO_v0.2.f3d, SO_v0.2_5inch_arm_hole_4mm_4x.dxf, SO_v0.2_6inch_arm_hole_4mm_4x.dxf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]
2018-09-27 v0.2 accessories
    added v0.2 accessories
    [SO_v0.2_battery_pad_bottom.dxf, SO_v0.2_battery_pad_top.dxf, SO_v0.2_pod_plate.dxf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]
2018-10-02 added press insert nut drawing
    added press insert nut drawing
2018-10-03 fixed 20x20 holes
    [SO_v0.2_center_plate_3mm.dxf]
2018-10-03 added M3 thread to model
2018-10-03 added "M3x10" & "M3x14" screws and new "press insert nut" model
    [SO_v0.2.f3d]
2018-10-04 added assembled model as .STEP
    [SO_v0.2_assembled.step]
2018-10-04 added assembled model as .STL
2019-07-21 uploaded v3 files
    [SO_v03.f3d, SO_v3_5inch_arm_4mm_4x.dxf, SO_v3_7inch_arm_6mm_4x.dxf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]
2019-11-10 Rename SO_v3_7inch_dead_cat_arm_4mm_4x.dxf to SO_v3_7inch_dead_cat_arm_6mm_4x.dxf
    renamed deadcat arms from 4mm to 6mm
    [SO_v3_7inch_dead_cat_arm_6mm_4x.dxf]
2021-01-01 added v4 files
    [SO_v4_5inch_arm_4mm_4x.dxf, SO_v4_7inch_arm_6mm_back_2x.dxf, SO_v4_7inch_arm_6mm_front_2x.dxf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]
2021-01-01 added .step file
    [So1-V4-2020-DEC-07-3D.STEP]
2021-01-01 added Fusion360, .IGS and .STEP files
    [SO_v4.STEP, SO_v4.f3d, SO_v4.igs]
